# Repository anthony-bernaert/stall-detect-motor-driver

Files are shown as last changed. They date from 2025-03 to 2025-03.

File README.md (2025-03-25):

# Motor Driver with Stall Detection
This motor driver safely operates small, brushed 5-24V DC motors up to 2A. It has current-based stall detection that automatically stops driving the motor when the end of travel or an excessive load is sensed.

The board has two inputs that make the motor spin in either direction. When a stall condition is detected, the motor is disabled until both inputs are released. This prevents the stalled motor from heating up and causing the windings to burn out.

In many situations, this removes the need to install mechanical or optical end-stops.

The circuit is built around a DRV8251A motor driver IC, with a few filters and discrete logic components.

>[!NOTE]
>This board was originally intended to be operated by physical buttons. Speed control through PWM is not supported.

## Features
- Robust DRV8251A motor driver chip
- Detects end of travel without adding mechanical or optical end-stops using motor stall current detection
- Operated by two (active-low) inputs, one for each motor direction
- LED indication for both inputs, and for stall conditions
- Simple setup: no microcontroller, no firmware
- Stall threshold, filtering and current limit tuneable with a set of trimpots
- Extra on-board fuse, as a fail-safe
- Open-drain stall status output

## Build overview



Navigate to the releases section to obtain the latest schematic and production files.

## How it works
For an explanation on how the circuit works, see [this page](THEORY.md).

## How to use
### Connections
After assembling the board, power (5-24VDC) must be applied to J1 at pins 'VIN' and 'GND'. The motor leads are to be connected to the same connector, at the pins indicated by 'MOTOR'.

Inputs are to be connected to J2, on pins IN1 and IN2. Inputs are considered active when they are pulled to GND (active-low). If switches are used, place these between GND and IN1/IN2.

### Tuning
The circuit has to be tuned before use:
1. Set the I-LIM trimpot so that the voltage at TP2 matches following formula: $V_{TP2} = I_{max}R_{R6}\cdot 1575\cdot 10^{-6}$.<br />Here, $I_{max}$ is the current limit you want to use for your motor, and $R_{R6}$ is normally 1K. To be safe, you can take $I_{max}$ around the rated stall current of your motor.
2. Then, first turn the T-TRIP trimpot completely clockwise to set the trip time to the maximum
3. Turn the I-TRIP trimpot almost completely clockwise to set the trip current to a very low level
4. Tune the trip current<br />
   a. Be sure that the motor can spin freely<br />
   b. Use IN1/IN2 to spin the motor. If it stalls, release the button, turn I-TRIP a bit counter-clockwise and try again until it no longer stalls.<br />
   c. After finding an acceptable stall threshold, turn I-TRIP a bit more to have some margin.
5. Tune the trip time if necessary<br />
   a. To make the circuit detect stalls earlier, turn the T-TRIP time counter-clockwise<br />
   b. When reducing this time, it's possible that you need to increase the trip current from step 4 a bit, to filter out the initial current peak when the motor starts spinning.

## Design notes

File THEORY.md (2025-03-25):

# How it works
## Motor drive control
The control circuit consists of a DRV8251A motor driver, which has two inputs (IN1 and IN2) allowing to drive the motor as follows:
| IN1 | IN2 | Action |
|-----|-----|---|
| 0 | 0 | Coast |
| 1 | 0 | Spin (normal)  |
| 0 | 1 | Spin (reverse) |
| 1 | 1 | Brake |

During normal operation, the user buttons directly control the IN1 and IN2 inputs of the chip. However, during stall conditions, the buttons are overruled: IN1 and IN2 are forced to zero in this case, resulting in the motor to 'coast' (which means: it is not actively driven).

The input circuit for user button 1 looks like this (a copy of this circuit is used for the other button):



The input signal SW1_N is assumed to be active-low and has a pull-up (R1). Furthermore, there is a TVS diode (D6) against EMI surges and a low-pass filter (R16/C11) to filter noise and input bounce. It has a MOSFET acting as an inverter (Q1) to accommodate for the IN1/IN2 polarity of the motor driver, and a status LED (D1). Voltage divider R3/R4 ensures the input voltage at SW1 (0-9V) is scaled down to keep the input voltage on IN1 within the allowed input range (0-5.5V) of the DRV8251A. Series resistor R3 also allows to safely short IN1 to ground (using N-channel MOSFET Q2) and overrule the pin during stall events. 

## Stall detection
The DRV8251A chip internally uses [current mirrors](https://en.wikipedia.org/wiki/Current_mirror) to eliminate the need for shunt resistors to measure instantaneous motor current. It has an output pin called "IPROPI" through which a current flows that is proportional to the instantaneous motor current (scaling factor: 1575 µA/A typ.).



Using Ohm's law, the output current of this pin can easily be converted to a voltage by placing a parallel resistor to ground. The voltage on this pin now becomes 

$`V_{IPROPI} = \frac{IPROPI}{R_{IPROPI}}`$,

or, calculated back into the actual motor current:
$`I_{\mathrm{motor}} = \frac{V_{IPROPI}}{R_{IPROPI} \cdot {1575 \cdot 10^{-6}}}`$

This is fed to a comparator which defines a hard threshold between 'stalled' and 'not stalled'. The output of the comparator is high (9V) when V+ > V-, and 0V otherwise. V- is the voltage proportional to the motor current, and V+ defines the 'trip current'. So, when the motor current is higher than the trip current, the output of the comparator becomes LOW.



The comparator output is then connected through an RC filter to a 555 chip. The filter is required to smooth out glitches and initial current peaks when the motor starts spinning. Note that if you don't include this filter, the stall circuit would trigger immediately when you press a button!

The 555 chip is used as 'set-reset' flip flop. This means the output is high (and stays high) whenever the 'trigger' input gets below 1/3 of the supply voltage (so here: 3V), and becomes low when the 'threshold' pin gets higher than 2/3 of supply voltage (here: 6V). So, in essence, the 'trigger' input acts as an inverted 'set' signal of a regular flip flop, while the 'threshold' pin acts as the reset signal of the flip flop.

In this circuit, the trigger pin falls below 3V when the comparator indicates an overcurrent condition during a sufficiently long period. When this happens, the 'STALL' signal becomes and remains active despite the motor getting disabled and soon not drawing current anymore.

To make the STALL signal inactive again, the 'threshold' pin needs to rise to a voltage of at least 6V. Due to the N-channel MOSFETs at the bottom of the circuit, the threshold pin sees a low voltage as soon as one of the user inputs are active. Both buttons must be released to allow the pin to charge (through an RC low-pass filter) back to a voltage higher than 6V.

This mechanism effectively stops the motor until new button presses.

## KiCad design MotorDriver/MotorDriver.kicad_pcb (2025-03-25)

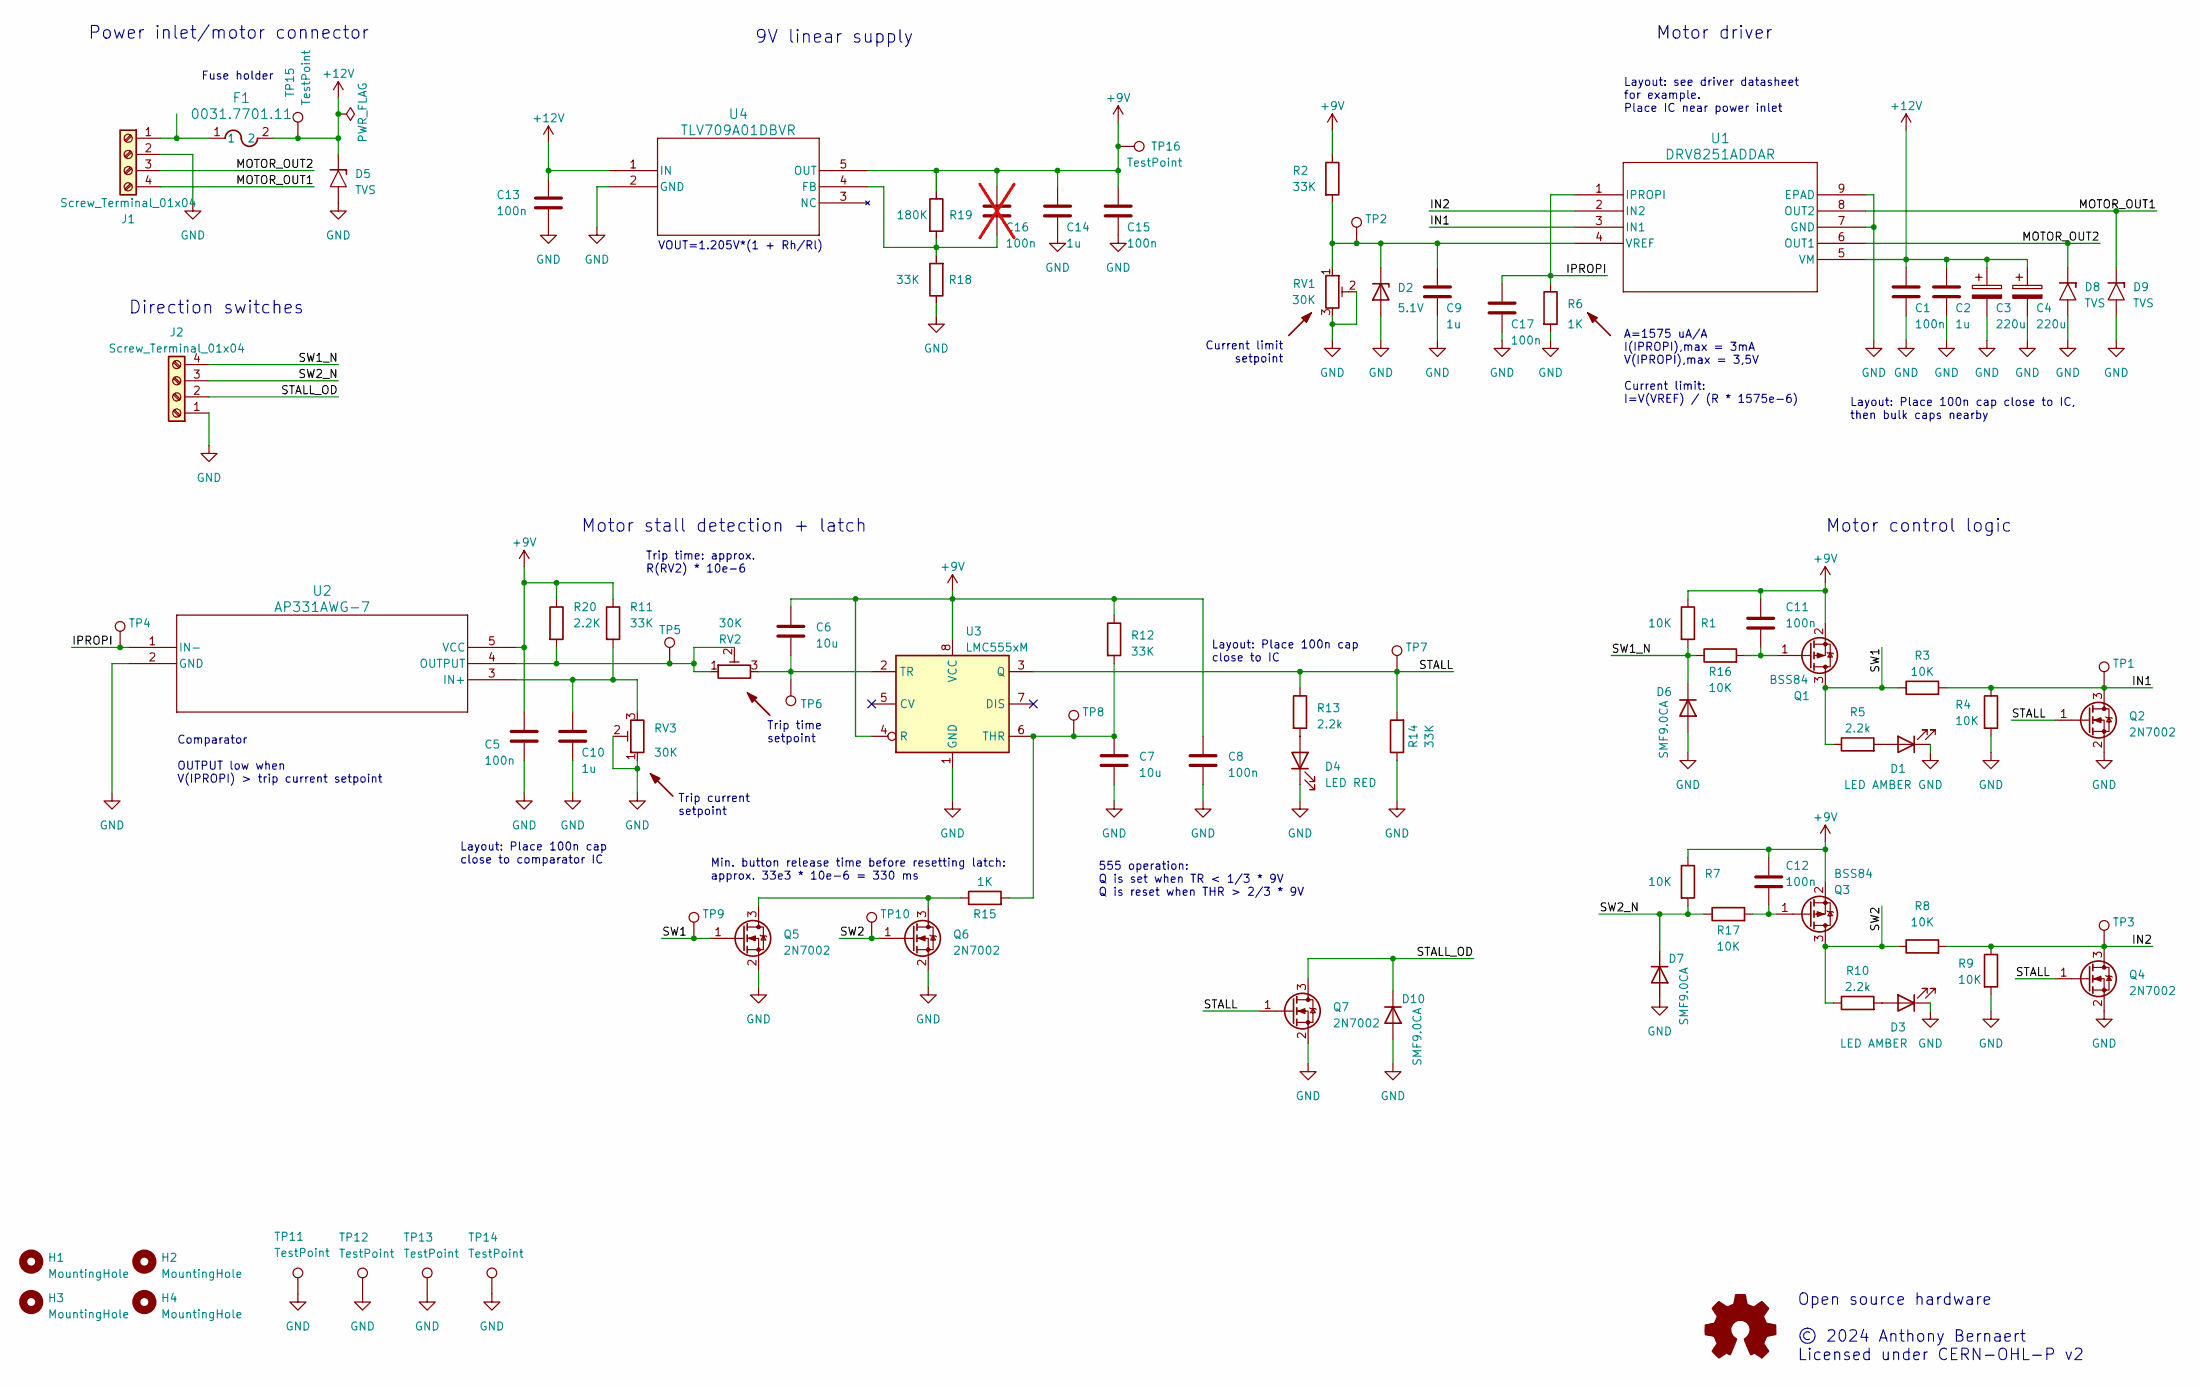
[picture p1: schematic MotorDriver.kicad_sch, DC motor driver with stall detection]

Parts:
C1, C5, C8, C11, C12, C13, C15, C17: 100n; C_1206_3216Metric
C2, C9, C10, C14: 1u; C_1206_3216Metric
C3, C4: 220u; CP_Elec_8x10; LCSC C278406
C6, C7: 10u; C_1206_3216Metric
C16: 100n; C_0603_1608Metric; not fitted
D1, D3: LED AMBER; LED_0603_1608Metric; LCSC C5656657
D2: 5.1V; D_SOD-123; LCSC C85181
D4: LED RED; LED_0603_1608Metric; LCSC C965799
D5, D8, D9: TVS; P25_DO-214AC_SMA; LCSC C1974908
D6, D7, D10: SMF9.0CA; D_SOD-123; LCSC C19077504
F1: 0031.7701.11; FUSE_0031.7701.11_SCH
H1, H2, H3, H4: MountingHole; MountingHole_3.5mm
J1, J2: Screw_Terminal_01x04; TerminalBlock_Phoenix_MKDS-1,5-4-5.08_1x04_P5.08mm_Horizont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
Q1, Q3: BSS84; SOT-23; LCSC C82079
Q2, Q4, Q5, Q6, Q7: 2N7002; SOT-23; LCSC C65189
R1, R3, R4, R7, R8, R9, R16, R17: 10K; R_0603_1608Metric
R2, R11, R12, R14, R18: 33K; R_0603_1608Metric
R5, R10, R13: 2.2k; R_0603_1608Metric
R6, R15: 1K; R_0603_1608Metric
R19: 180K; R_0603_1608Metric
R20: 2.2K; R_0603_1608Metric
RV1, RV2, RV3: 30K; Potentiometer_Bourns_TC33X_Vertical; LCSC C6331330
TP1, TP2, TP3, TP4, TP5, TP6, TP7, TP8, TP9, TP10: TestPoint; TestPoint_Pad_D1.5mm
TP11, TP12, TP13, TP14, TP15, TP16: TestPoint; Pin_D1.0mm_L10.0mm
U1: DRV8251ADDAR; SOIC8_DDA_TEX; LCSC C5218844
U2: AP331AWG-7; SOT25_DIO; LCSC C151034
U3: LMC555xM; SOIC-8_3.9x4.9mm_P1.27mm; LCSC C90760
U4: TLV709A01DBVR; SOT-23-5_DBV_TEX; LCSC C22365366

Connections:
+9V: C5.1, C6.1, C8.1, C11.1, C12.1, C14.1, C15.1, C16.1, Q1.2 (S), Q3.2 (S), R1.1, R2.1, R7.1, R11.1, R12.1, R19.1, R20.1, TP16.1, U2.5 (VCC), U3.4 (R), U3.8 (VCC), U4.5 (OUT)
+12V: C1.1, C2.1, C3.1, C4.1, C13.1, D5.1 (K), F1.2, TP15.1, U1.5 (VM), U4.1 (IN)
/IN1: Q2.3 (D), R3.2, R4.1, TP1.1, U1.3 (IN1)
/IN2: Q4.3 (D), R8.2, R9.1, TP3.1, U1.2 (IN2)
/IPROPI: C17.1, R6.1, TP4.1, U1.1 (IPROPI), U2.1 (IN-)
/MOTOR_OUT1: D9.1 (K), J1.4, U1.8 (OUT2)
/MOTOR_OUT2: D8.1 (K), J1.3, U1.6 (OUT1)
/STALL: Q2.1 (G), Q4.1 (G), Q7.1 (G), R13.1, R14.2, TP7.1, U3.3 (Q)
/STALL_OD: D10.1 (K), J2.2, Q7.3 (D)
/SW1: Q1.3 (D), Q5.1 (G), R3.1, R5.1, TP9.1
/SW1_N: D6.1 (K), J2.4, R1.2, R16.1
/SW2: Q3.3 (D), Q6.1 (G), R8.1, R10.1, TP10.1
/SW2_N: D7.1 (K), J2.3, R7.2, R17.1
GND: C1.2, C2.2, C3.2, C4.2, C5.2, C7.2, C8.2, C9.2, C10.2, C13.2, C14.2, C15.2, C17.2, D1.1 (K), D2.2 (A), D3.1 (K), D4.1 (K), D5.2 (A), D6.2 (A), D7.2 (A), D8.2 (A), D9.2 (A), D10.2 (A), J1.2, J2.1, Q2.2 (S), Q4.2 (S), Q5.2 (S), Q6.2 (S), Q7.2 (S), R4.2, R6.2, R9.2, R14.1, R18.1, RV1.2, RV1.3, RV3.1, RV3.2, TP11.1, TP12.1, TP13.1, TP14.1, U1.7 (GND), U1.9 (EPAD), U2.2 (GND), U3.1 (GND), U4.2 (GND)
unnamed: D1.2 (A), R5.2
unnamed: C9.1, D2.1 (K), R2.2, RV1.1, TP2.1, U1.4 (VREF)
unnamed: D3.2 (A), R10.2
unnamed: D4.2 (A), R13.2
unnamed: F1.1, J1.1
unnamed: C11.2, Q1.1 (G), R16.2
unnamed: C12.2, Q3.1 (G), R17.2
unnamed: Q5.3 (D), Q6.3 (D), R15.1
unnamed: C10.1, R11.2, RV3.3, U2.3 (IN+)
unnamed: R20.2, RV2.1, RV2.2, TP5.1, U2.4 (OUTPUT)
unnamed: C7.1, R12.2, R15.2, TP8.1, U3.6 (THR)
unnamed: C6.2, RV2.3, TP6.1, U3.2 (TR)
unnamed: C16.2, R18.2, R19.2, U4.4 (FB)

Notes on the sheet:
9V linear supply
Layout: see driver datasheet for example. Place IC near power inlet
Comparator OUTPUT low when V(IPROPI) > trip current setpoint
Current limit setpoint
Layout: Place 100n cap close to comparator IC
VOUT=1.205V*(1 + Rh/Rl)
Layout: Place 100n cap close to IC
Trip time setpoint
Motor driver
Power inlet/motor connector
Min. button release time before resetting latch: approx. 33e3 * 10e-6 = 330 ms
Trip time: approx. R(RV2) * 10e-6
555 operation: Q is set when TR < 1/3 * 9V Q is reset when THR > 2/3 * 9V
Direction switches
Open source hardware © 2024 Anthony Bernaert Licensed under CERN-OHL-P v2
Motor stall detection + latch
Layout: Place 100n cap close to IC, then bulk caps nearby
Trip current setpoint
Fuse holder
A=1575 uA/A I(IPROPI),max = 3mA V(IPROPI),max = 3,5V Current limit: I=V(VREF) / (R * 1575e-6)
Motor control logic

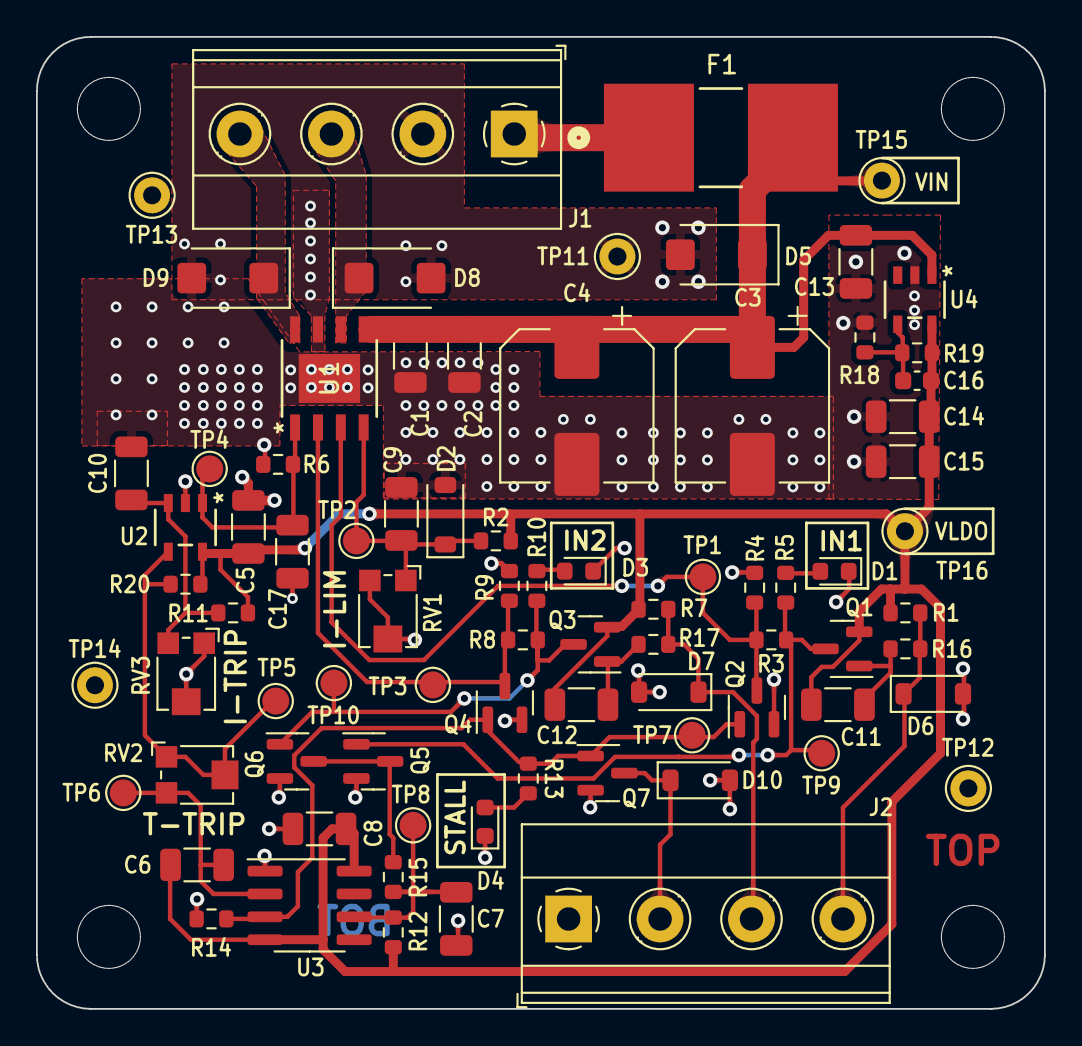
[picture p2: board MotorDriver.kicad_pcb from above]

Board: 2 copper layers, 56.0 x 54.0 mm, 84 parts (0 on the bottom side), 27 nets.

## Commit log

2024-11-04 Add gitignore for KiCad project
2024-11-04 Check-in of first revision
    [MotorDriver.kicad_pcb, MotorDriver.kicad_sch]
2025-03-25 Add LCSC order numbers
    [MotorDriver.kicad_pcb, MotorDriver.kicad_sch]

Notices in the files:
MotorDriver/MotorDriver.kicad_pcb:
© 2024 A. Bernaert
